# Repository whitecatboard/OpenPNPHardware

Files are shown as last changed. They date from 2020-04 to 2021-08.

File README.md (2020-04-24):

# Introduction

[Whitecat](https://whitecatboard.org) was created in 2016 as an ecosystem to provide hardware and software to everyone to deploy real IOT use cases in an easy way. Once the hardware was designed, we had to decide how to assemble it, and after analyzing various options we decided that, in a first stage, the best way was to produce our own units. Due to that, we started the construction of our own Pick&Place machine, based on [OpenBuilds](https://openbuilds.com), [OpenPNP](http://openpnp.org), and some custom hardware.

On this repository you will find all the relevant information about our P&P machine, such as custom hardware, 3D printed parts models, and more.

## Project parts

* The machine
* Control board
* [Feeders](https://github.com/whitecatboard/OpenPNPHardware/tree/master/feeder)

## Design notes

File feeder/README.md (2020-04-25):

# Introduction

Feeders have the responsibility to supply components to the machine. To have a high quality, in all the pick & place process, it's mandatory that feeders supply components in a reliable and precise way. Supplying a component is the first step of the pick & place process, so , the more precission on feeders, the more precission on the final place possition, because less corrections will be required in the next steps.

If you have enough money, you can buy feeders used in the industry by US $130 each. This was not our case, because:

* We need to mount at least 40 feeders on our machine, and we don't have US $5,200.
* Usually these feeders are pneumatic feeders, and a lot of additional noisy hardware is required (more money).

For the above reasons, we decided to work in our own feeder solution, after reviewing the [Volker Besmens's project](https://www.vbesmens.de/en/pick-and-place/automatic-feeder.html).

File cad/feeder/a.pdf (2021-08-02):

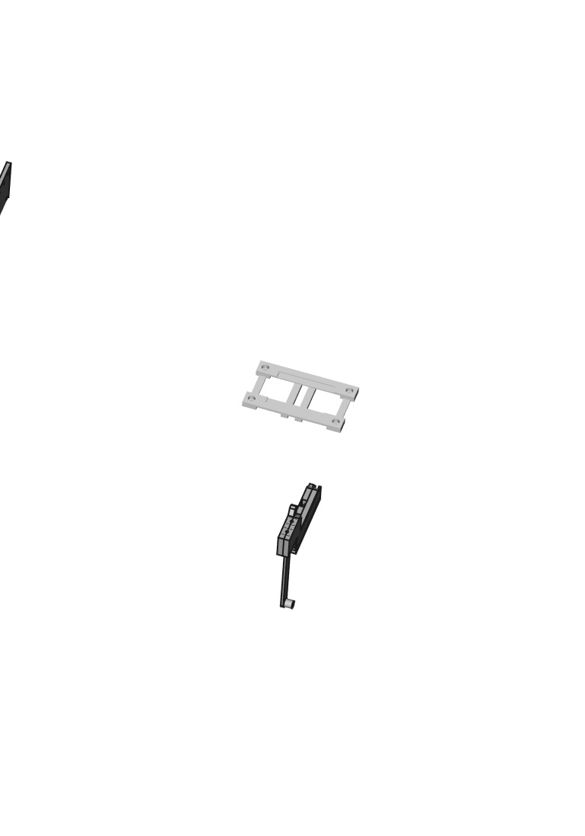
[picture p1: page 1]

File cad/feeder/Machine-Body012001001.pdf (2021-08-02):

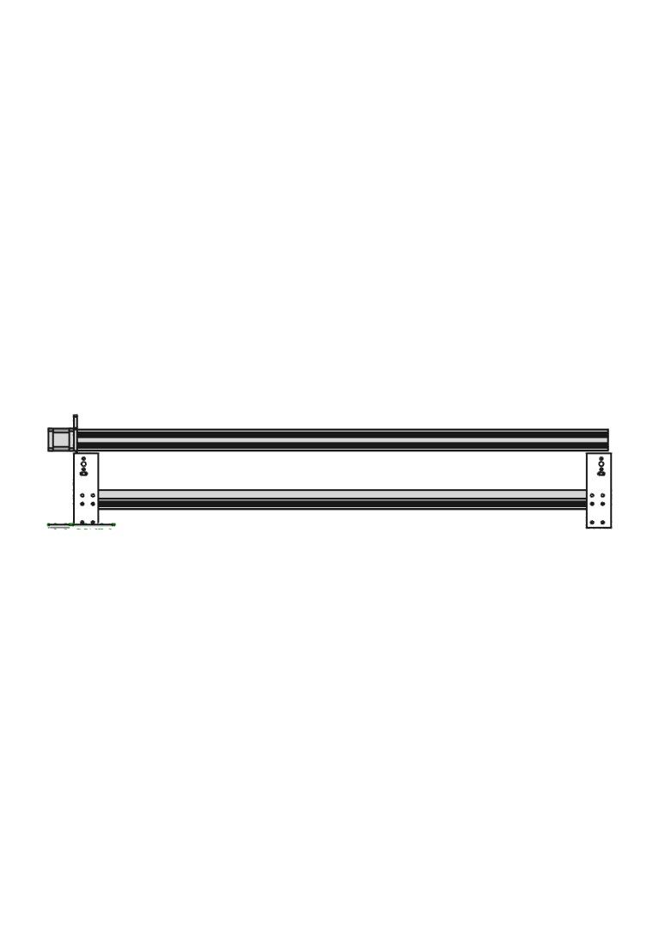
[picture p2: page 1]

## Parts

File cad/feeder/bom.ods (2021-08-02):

Description | Unit Price | Units | Total | Category
V-Slot 20x40x500mm Linear Rail | 6.06 | 4 | 24.23 | Frame
V-Slot 20x20x1000mm Linear Rail | 8.83 | 2 | 17.65 | Frame
V-Slot 20x40x1000mm Linear Rail | 12.11 | 1 | 12.11 | X-Axis
V-Slot 20x80x1000mm Linear Rail | 18.70 | 4 | 74.81 | Bed
12V Power Supply 33A 400W | 29.78 | 1 | 29.78 | Electronics
24V Power Supply 17A 400W | 39.48 | 1 | 39.48 | Electronics
NEMA 17 Stepper Motor 1.68A Bipolar 4 wires 77oz | 14.05 | 4 | 56.20 | Electronics
 |  |  | 254.26

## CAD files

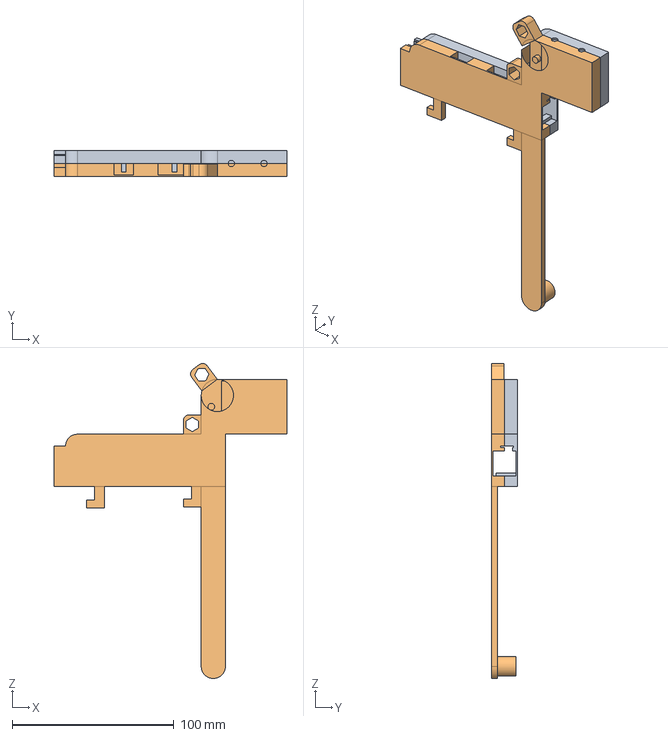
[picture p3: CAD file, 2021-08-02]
cad/feeder/Feeder2-Body001002Boolean.step
144.0 x 16.0 x 195.0 mm
Right001
Left001

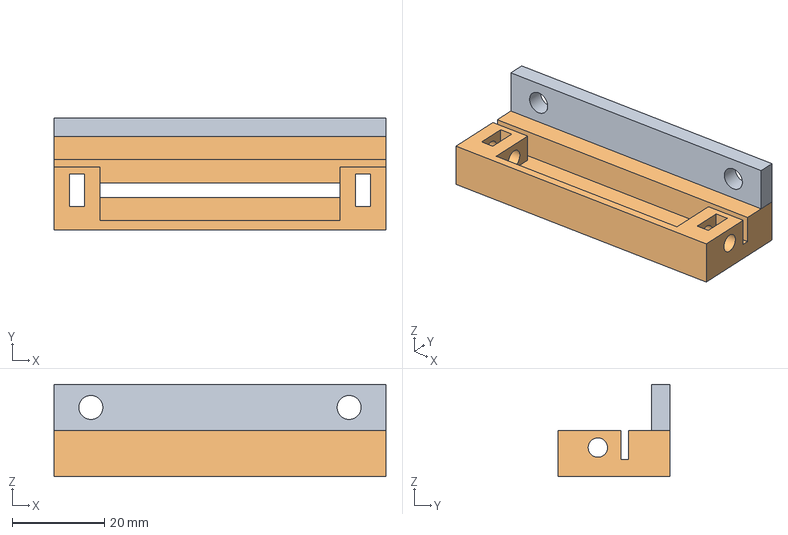
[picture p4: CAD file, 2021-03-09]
cad/head/BeltTensor.step
72.0 x 24.2 x 20.0 mm

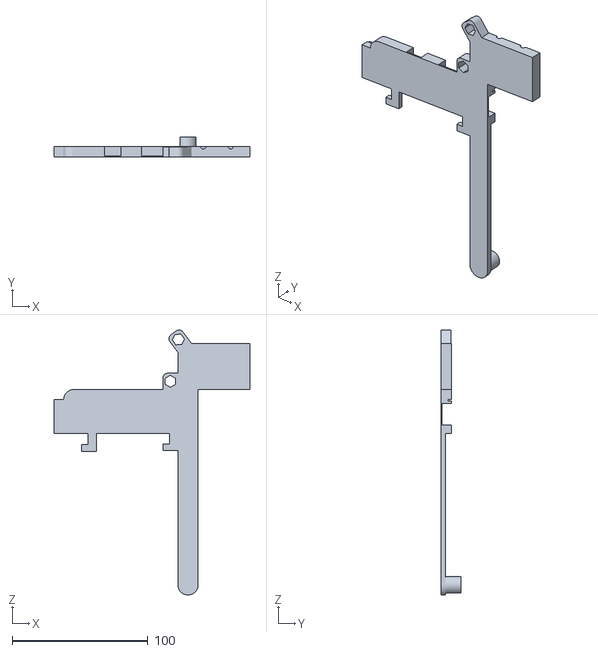
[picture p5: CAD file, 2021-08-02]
feeder/stl/Feeder_8mm_Left_1.0_mm_tape.stl
144.0 x 15.0 x 195.0

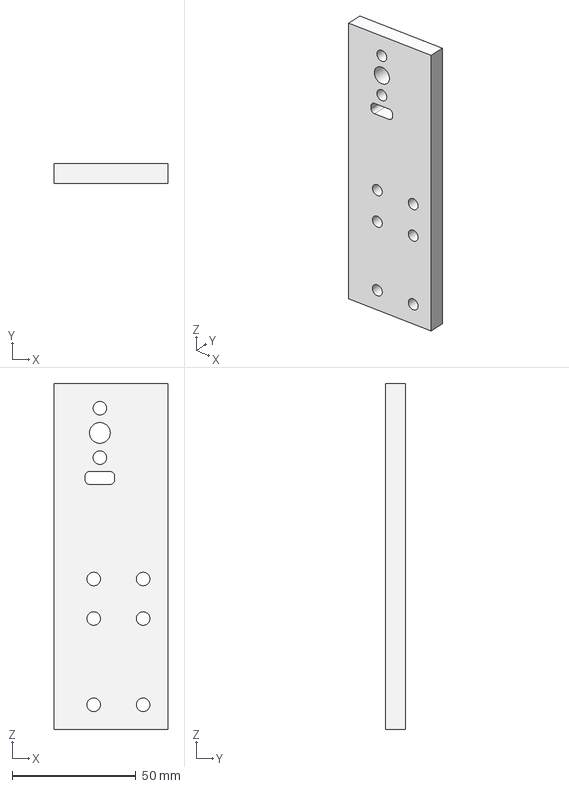
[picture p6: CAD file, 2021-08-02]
cad/feeder/WHC-DESK-PNP-FRM-PLT.step
46.0 x 8.00 x 140.0 mm

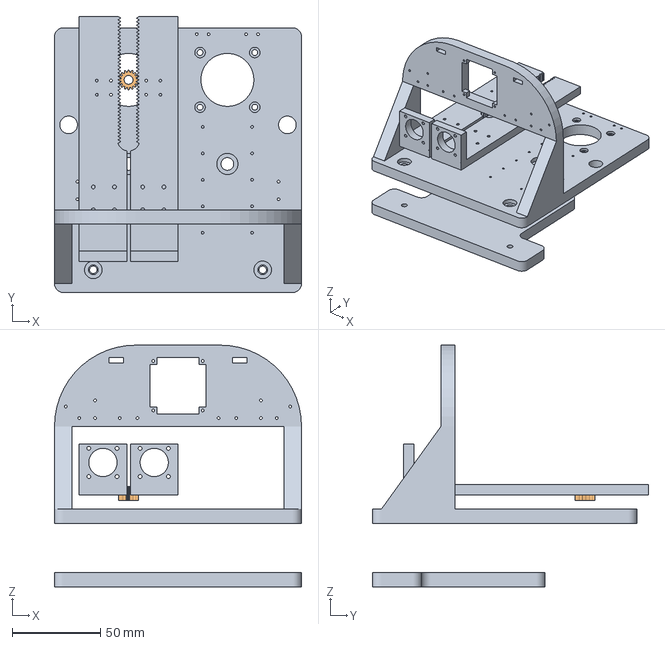
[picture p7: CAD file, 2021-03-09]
cad/head/Head.FCStd
140.0 x 156.4 x 137.0 mm
gear

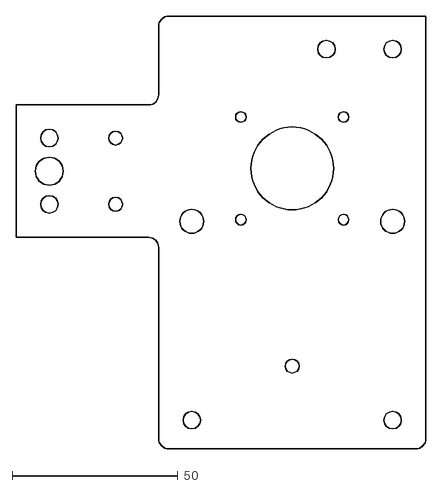
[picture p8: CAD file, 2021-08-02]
cad/feeder/Machine-X-Axis Plate.dxf
123.6 x 130.6

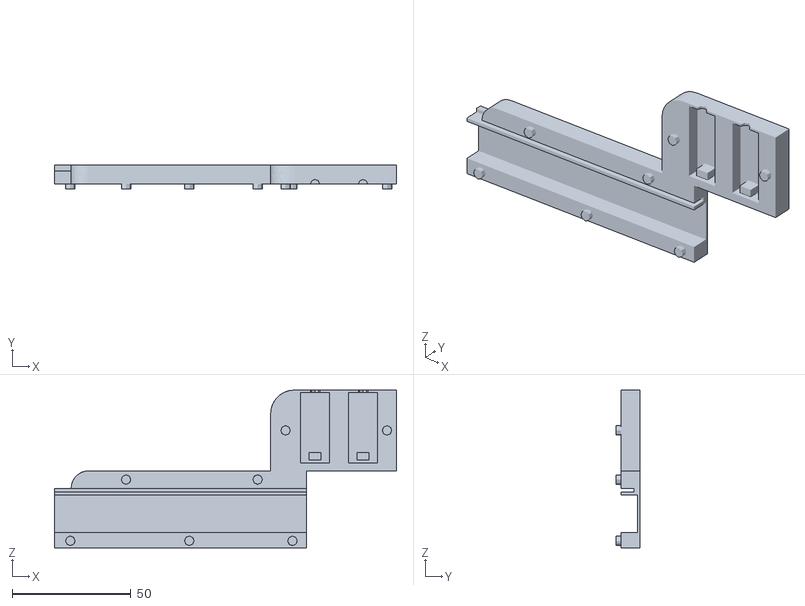
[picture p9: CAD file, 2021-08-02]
feeder/stl/Feeder_8mm_Right_1.5_mm_tape.stl
144.0 x 10.0 x 66.5

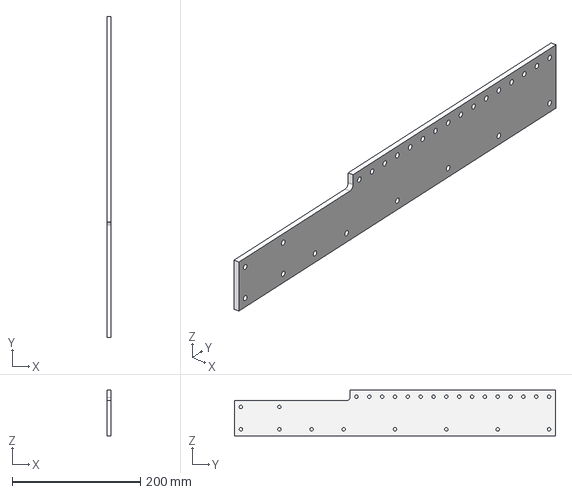
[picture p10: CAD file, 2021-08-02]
cad/feeder/Side Cover.step
6.00 x 500.0 x 70.9 mm

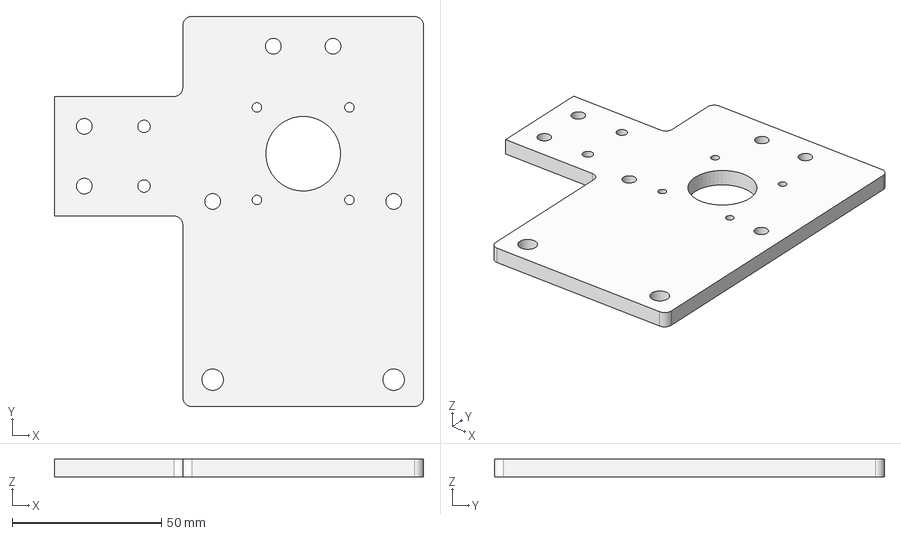
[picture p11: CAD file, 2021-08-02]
cad/feeder/Machine-Body012001001.step
123.6 x 130.6 x 6.00 mm

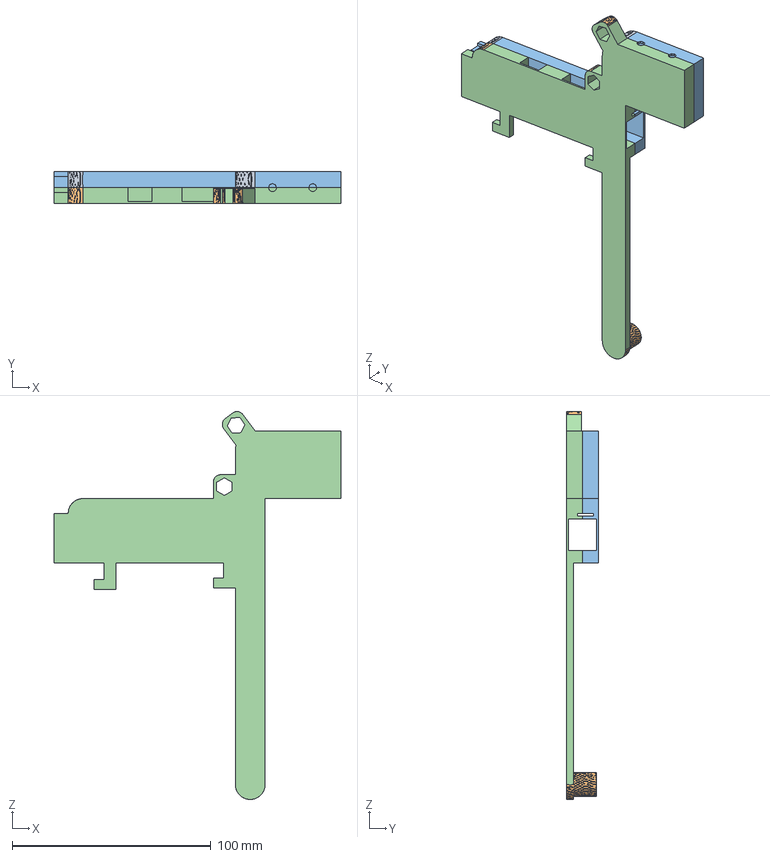
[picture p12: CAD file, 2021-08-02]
cad/feeder/Feeder2.FCStd
144.0 x 16.0 x 195.0 mm
Right001
Left001
Right001 (Meshed)
Left001 (Meshed)

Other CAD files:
feeder/stl/Feeder_8mm_Left_1.5_mm_tape.stl
feeder/stl/Feeder_8mm_Right_0.6_mm_tape.stl
feeder/stl/Feeder_8mm_Right_1.0_mm_tape.stl
cad/feeder/WHC-DESK-PNP-SIDE-COV.step
feeder/stl/Feeder_8mm_Left_1.2_mm_tape.stl
feeder/stl/Feeder_8mm_Right_1.2_mm_tape.stl
cad/feeder/Plate.step
feeder/stl/Feeder_8mm_Left_0.6_mm_tape.stl
cad/feeder/Machine-Body012001001.dxf
cad/feeder/Machine-Front Left Plate Frame001.dxf
cad/feeder/bed.step
feeder/stl/Cover_Tape_Reel_8mm.stl
feeder/stl/Feeder_8mm_Frame_fix.stl
feeder/stl/Feeder_8mm_Power_Supply_Frame_Fix.stl
feeder/stl/Tape_Reel_Stop.stl

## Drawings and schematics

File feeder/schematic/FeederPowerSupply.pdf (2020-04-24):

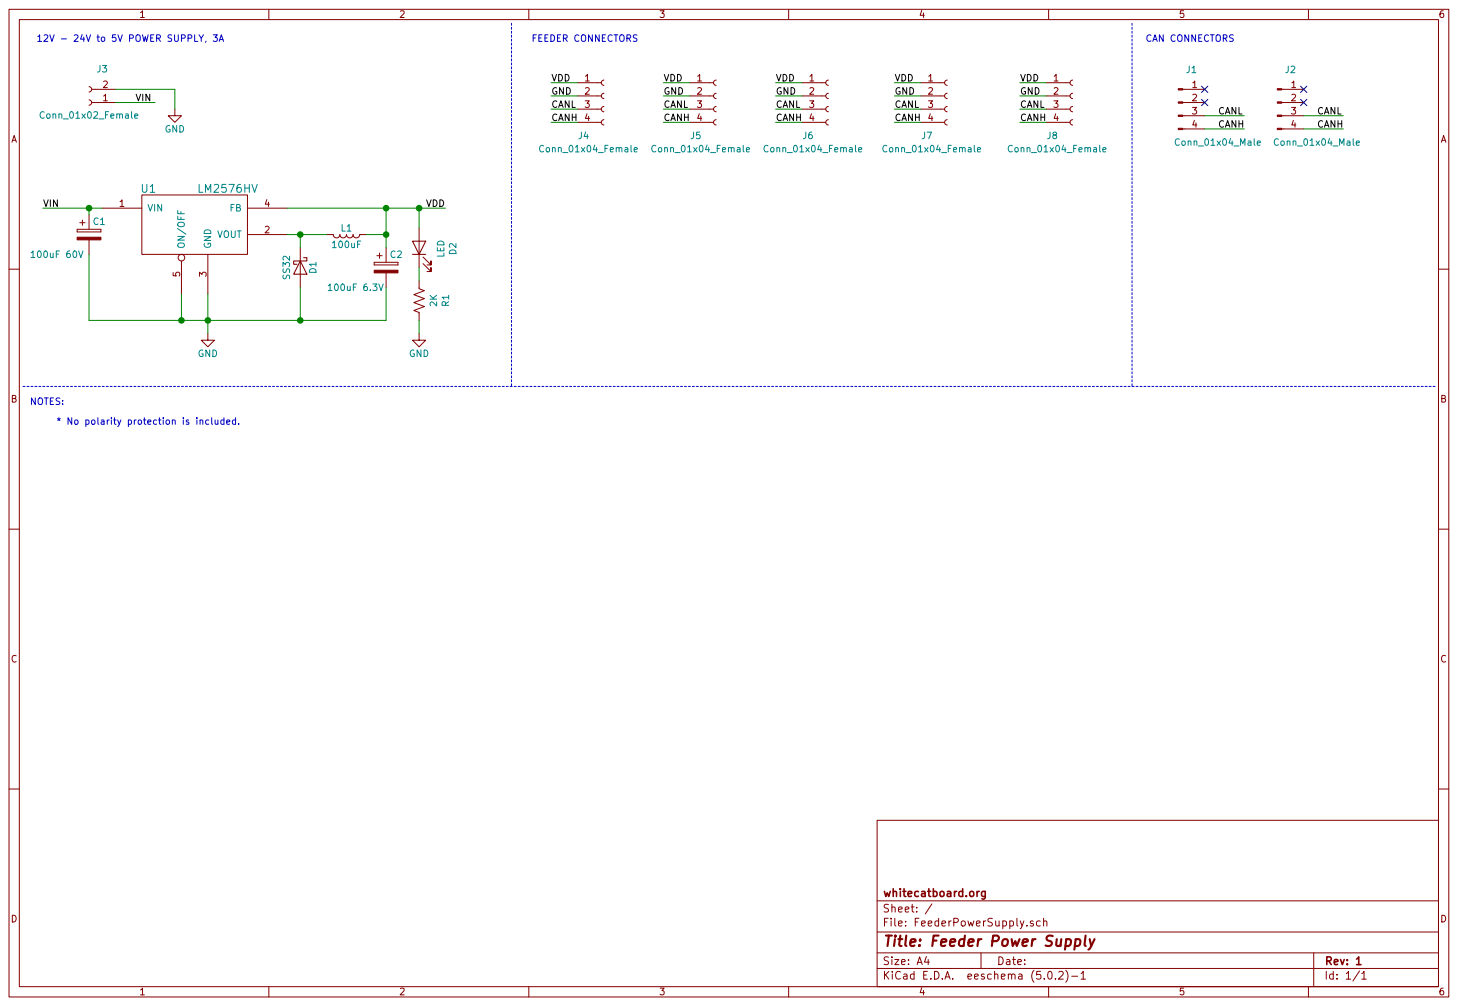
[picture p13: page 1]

J2 Conn_01x04_Male CANL CANH D2 LED 2KR1 GND

File: FeederPowerSupply.sch Sheet: / whitecatboard.org

Id: 1/1 Title: Feeder Power Supply

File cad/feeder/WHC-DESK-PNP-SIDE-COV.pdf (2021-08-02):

# All holes are non-threaded trough M5 holes

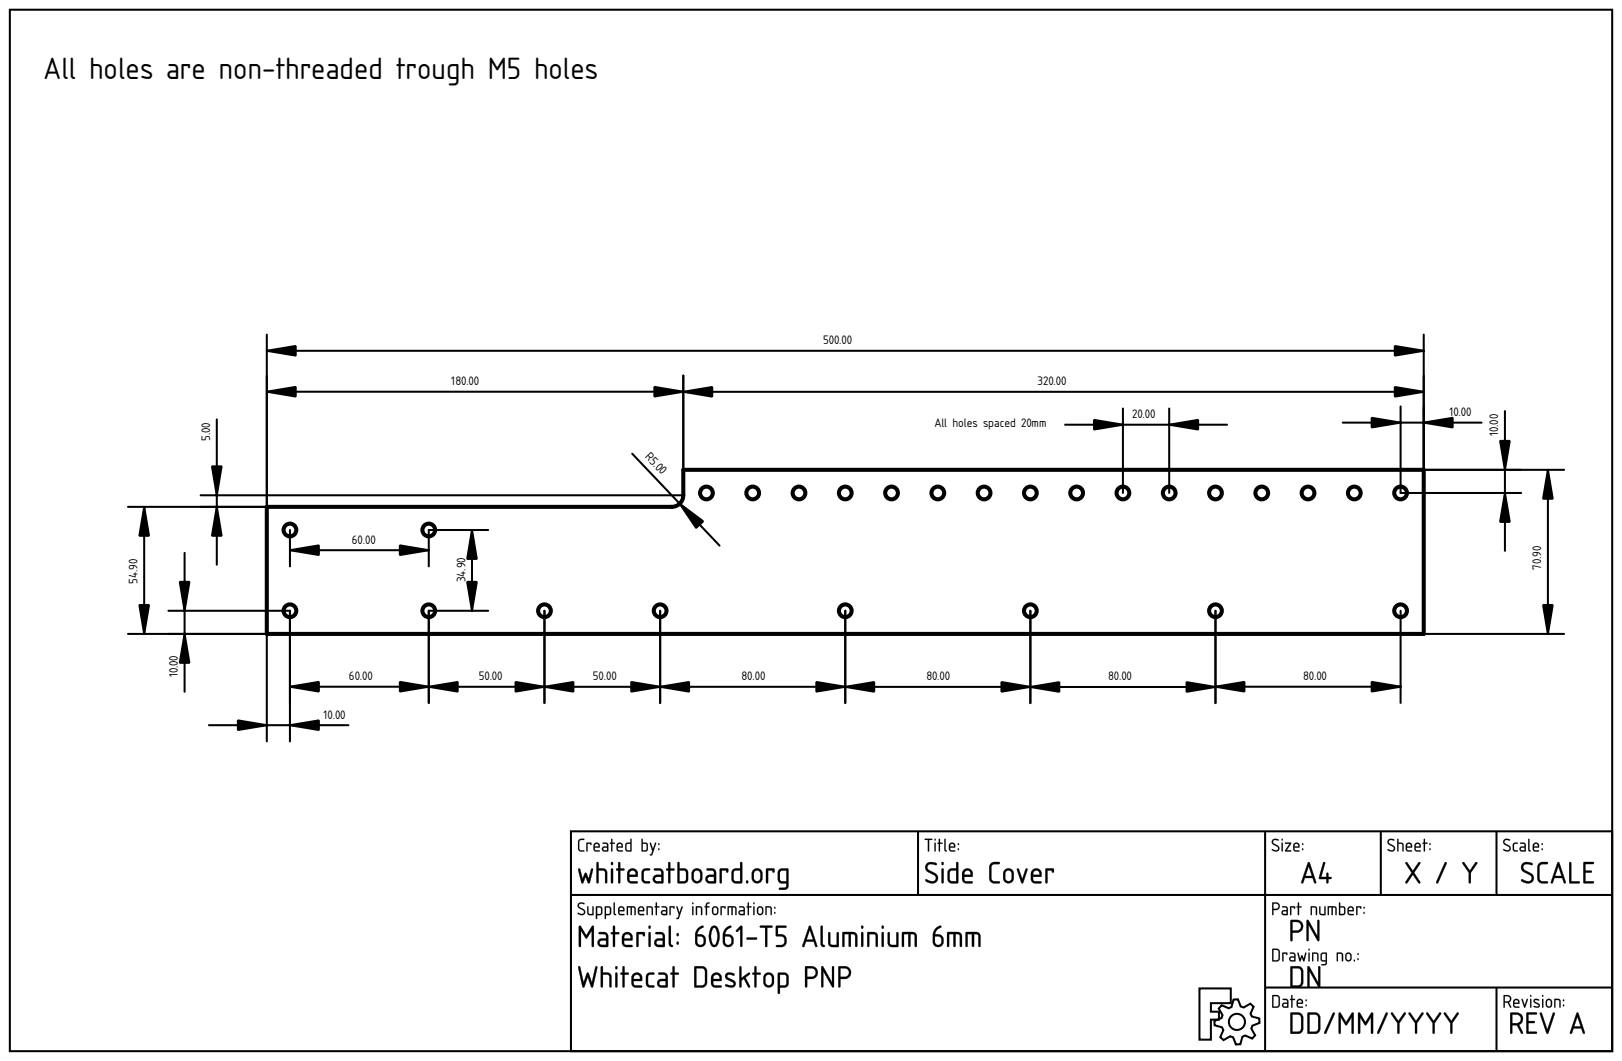
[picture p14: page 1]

All holes spaced 20mm

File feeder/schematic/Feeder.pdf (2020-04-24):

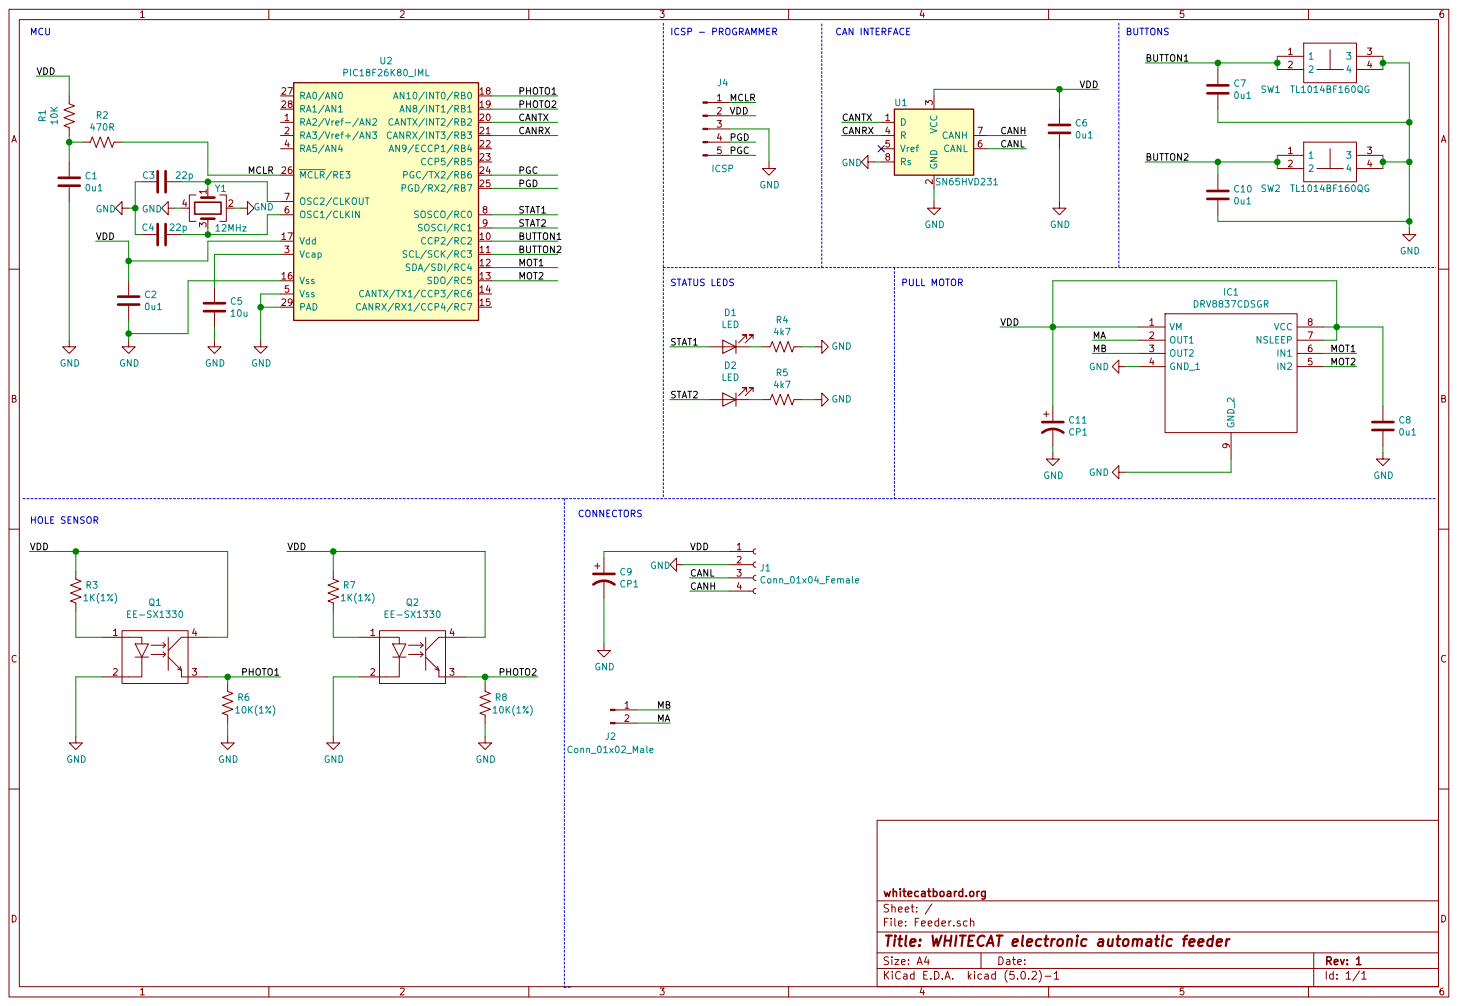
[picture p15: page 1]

Id: 1/1 Title: WHITECAT electronic automatic feeder File: Feeder.sch Sheet: / whitecatboard.org

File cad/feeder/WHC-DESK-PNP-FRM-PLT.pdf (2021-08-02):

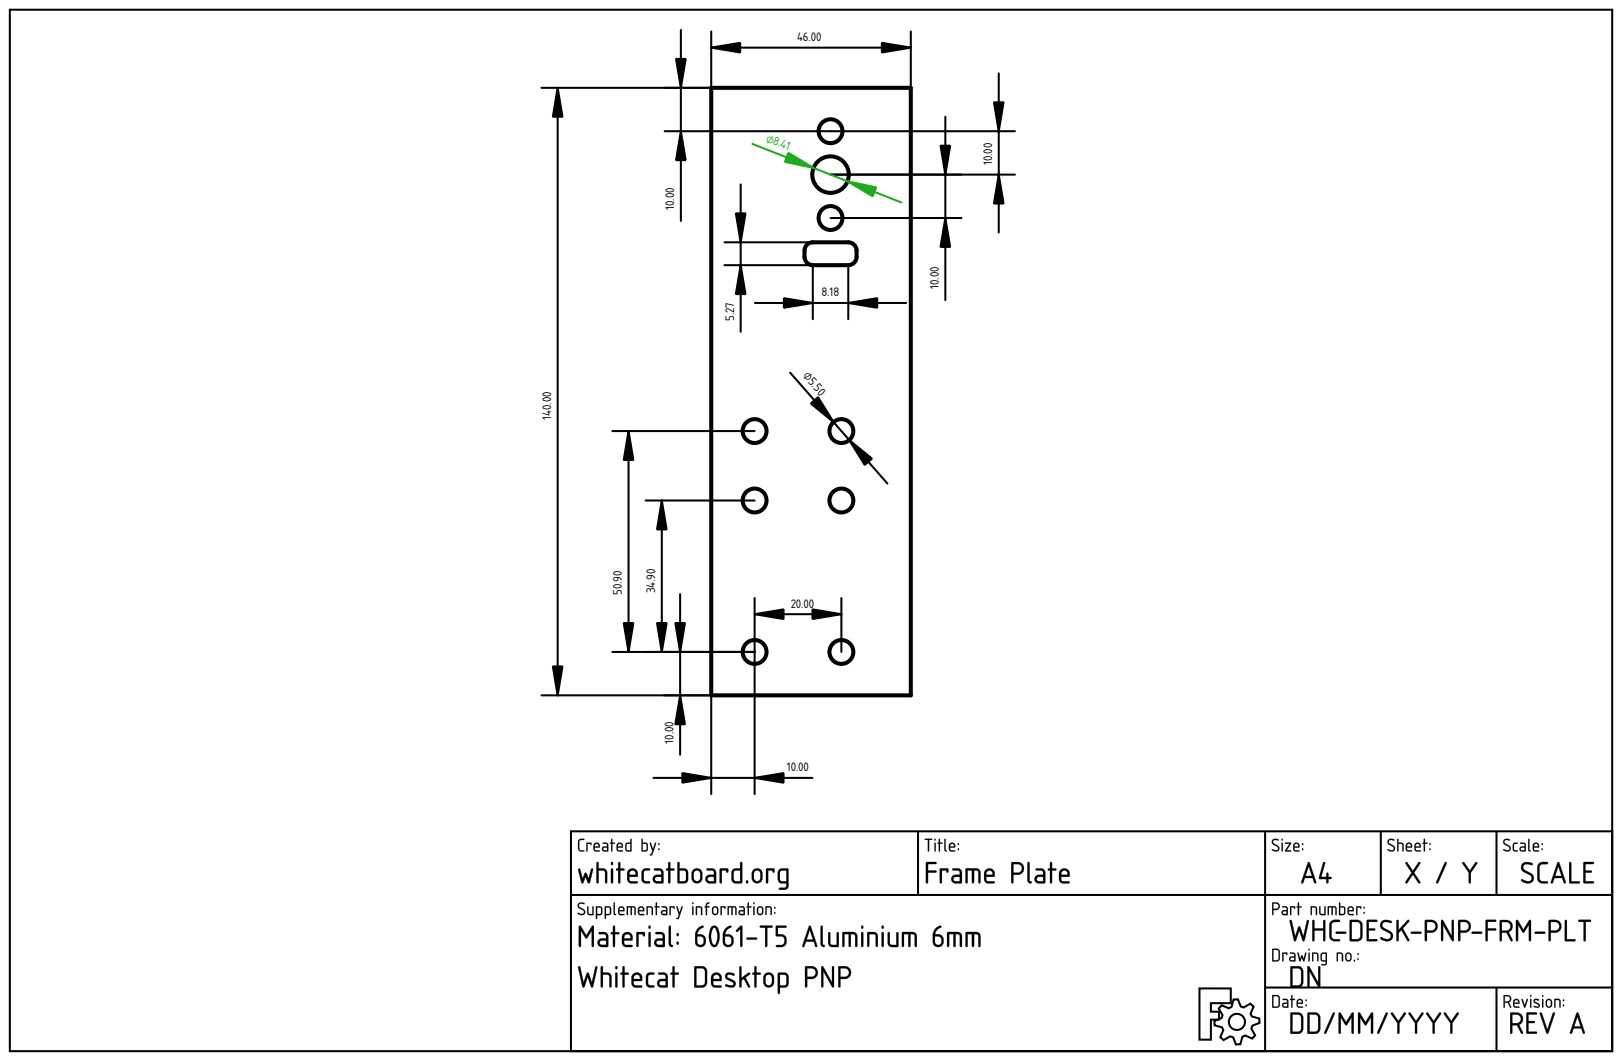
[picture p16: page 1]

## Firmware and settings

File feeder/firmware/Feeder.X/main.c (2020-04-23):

/*
 *          /\       /\
 *         /  \_____/  \
 *        /_____________\
 *        W H I T E C A T
 *
 * Copyright (C) 2020, IBEROXARXA SERVICIOS INTEGRALES, S.L.
 * Copyright (C) 2020, Jaume Olivé Petrus (jolive@whitecatboard.org)
 *
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
 * You should have received a copy of the GNU General Public License
 * along with this program.  If not, see <http://www.gnu.org/licenses/>.
 */

#include "gpio.h"
#include "can.h"
#include "task.h"
#include "motor.h"
#include "eeprom.h"

#include <xc.h>
#include <string.h>
#include <stdint.h>

// If no hole is detected within this time a feeder error will be triggered
#define FEED_TIMEOUT 1500

// EEPROM data
#define FEEDER_ID      0x0000 // Feeder id
#define FEEDER_PITCH   0x0001 // Feeder pitch
#define FEED_OK        0x0002 // Number of feed request OK
#define FEED_ERR       0x0006 // Number of feed request ERR

// Hardware mapping
#define STAT1_LED C0 // STAT1 led
#define STAT2_LED C1 // STAT2 led
#define MOTOR_CW  C5 // CW pin
#define MOTOR_CCW C4 // CCW pin
#define BUTTON1   C2 // Button 1
#define BUTTON2   C3 // Button 2
#define SWITCH1   B0 // Switch 1
#define SWITCH2   B1 // Switch 2

// Feeder status
typedef enum {
    StatusUnknown = 1,
    StatusPrevious = 2,
    StatusNotConfigured = 3,
    StatusWaitForConfig = 4,
    StatusReady = 5,
    StatusOnFeed = 6,
    StatusOnUnroll = 7,
    StatusDuplicatedId = 8,
} feeder_status_t;

// Feeder pitch types
typedef enum {
    Pitch_1_2 = 1, // Pitch 0.5
    Pitch_1,       // Pitch 1
    Pitch_2,       // Pitch 2
    Pitch_3,       // Pitch 3
    Pitch_4,       // Pitch 4
} feeder_pitch_t;

// Can message types
#define SERVICE_MSG 0x100
#define FEED_MSG    0X200
#define RESP_MSG    0x300
#define COUNT_MSG   0x301

// Service message
typedef enum {
    ServiceSetId = 1,
    ServiceSetPitch = 2,
    ServiceUpdate = 3,
    ServiceSaveCounters = 4,
    ServiceGetCounters = 5,
    ServiceResetCounters = 6,
} service_msg_type_t;

typedef struct {
    service_msg_type_t type; // Type of service message
    uint8_t data0;           // Message data 0
    uint8_t data1;           // Message data 1
} service_msg_t;

// Feed message
typedef struct {
    uint8_t feeder_id; // Feeder to perform feed operation
} feed_msg_t;

typedef struct {
    uint8_t feeder_id; // Feeder that has performed a feed operation
    uint8_t status;    // Feed operation status. 1 = ok, 0 = error
} feed_msg_response_t;

// Counter message
typedef struct {
    uint8_t feeder_id;
    uint8_t counter_id; // 1 = feed_ok, 2 = feed_err
    uint32_t value;
} counters_msg_t;

extern uint16_t _time_delta;
extern uint16_t _time_delta_led;
extern uint16_t _time_delta_button;

static uint8_t feeder_id = 0x00;
static feeder_pitch_t feeder_pitch = 0;

// Feeder status
static feeder_status_t status = StatusNotConfigured;
static feeder_status_t prev_status = StatusNotConfigured;

// Number of holes detected on current feed operation
static uint8_t detected_holes = 0;

// Number of holes required to get the next component for a feed operation
static uint8_t pitch_holes = 0;

// Counters
static uint32_t feed_ok = 0;
static uint32_t feed_err = 0;

static void update_status(feeder_status_t new_status) {
    if (new_status == StatusUnknown) {
        if (status != StatusDuplicatedId) {
            if ((feeder_id == 0) || (feeder_id == 0xff)) {
                if (status != new_status) {
                    prev_status = status;
                }
                
                status = StatusNotConfigured;
            } else {
                prev_status = StatusReady;
                status = StatusReady;
            }             
        }
        
        if ((feeder_pitch == 0) || (feeder_pitch == 0xff)) {
            // Default pitch
            feeder_pitch = Pitch_1;
            
            eeprom_write8(FEEDER_PITCH, feeder_pitch);
        }
        
        if (feed_ok == 0xffffffff) {
            feed_ok = 0;
        }
        
        if (feed_err == 0xffffffff) {
            feed_err = 0;
        }
    } else if (new_status == StatusPrevious) {
        status = prev_status;
    } else {
        if (status != new_status) {
            prev_status = status;
        }
        status = new_status;
    }
}

static uint8_t feed() {  
    uint8_t ok = 1;
    
    // Reset number of detected holes
    detected_holes = 0; 
    
    // Compute required number of holes to feed a component
    switch (feeder_pitch) {
        case Pitch_1_2: pitch_holes = 1; break;
        case Pitch_1:   pitch_holes = 1; break;
        case Pitch_2:   pitch_holes = 2; break;
        case Pitch_3:   pitch_holes = 3; break;
        case Pitch_4:   pitch_holes = 4; break;
    }    

    // Set timeout
    uint16_t timeout = FEED_TIMEOUT * pitch_holes;
    
    // Reset time
    _time_delta = 0;
    
    // Start move motor
    motor_ccw();

    while ((detected_holes < pitch_holes) && (ok)) {
        ok = _time_delta < timeout;
        
        asm("nop");
    }
    
    if (!ok) {
        // If timeout stop motor
        motor_stop();
    }    
    
    update_status(StatusPrevious);

    return ok;
}

static void unroll(void) {
    update_status(StatusOnUnroll);

    motor_cw();
    while (!gpio_pin_get(BUTTON2, 1));
    motor_stop();

    update_status(StatusPrevious);
}

static void process_feed_msg(can_frame_t *cf) {
    feed_msg_t msg;
    can_frame_t response;
    
    // Check that message size corresponds to a feed message
    if (cf->dlc == sizeof(feed_msg_t)) {
        // Get message
        memcpy(&msg, cf->data, cf->dlc);
        
        // Check that message is for us
        if (msg.feeder_id == feeder_id) {
            update_status(StatusOnFeed);    
            __delay_ms(5);
            task_disable();

            if (feed()) {
                feed_ok++;
                
                // Send response            
                response.sid = RESP_MSG;
                response.dlc = sizeof(feed_msg_response_t);
                response.data[0] = feeder_id;
                response.data[1] = 0x01;

                can_send(&response);                
            } else {
                feed_err++;
                
                // Send response            
                response.sid = RESP_MSG;
                response.dlc = sizeof(feed_msg_response_t);
                response.data[0] = feeder_id;
                response.data[1] = 0x00;

                can_send(&response);                                
            }
           
            task_enable();
        }
    }
}

static void process_service_msg(can_frame_t *cf) {
    service_msg_t msg;
    
    // Check that message size corresponds to a service message
    if (cf->dlc == sizeof(service_msg_t)) {
        // Get message
        memcpy(&msg, cf->data, cf->dlc);
        
        if ((msg.type == ServiceSetId) && (status == StatusWaitForConfig)) {
            feeder_id = msg.data0;
            
            eeprom_write8(FEEDER_ID, feeder_id);
            
            update_status(StatusUnknown);
        } else if ((msg.type == ServiceSetPitch) && (status == StatusReady)) {
            if (feeder_id == msg.data0) {
                feeder_pitch = msg.data1;
            
                eeprom_write8(FEEDER_PITCH, feeder_pitch);                
            }
        } else if ((msg.type == ServiceUpdate) && (status == StatusReady)) {
            if (msg.data0 == feeder_id) {
                asm("reset");
            }
        } else if ((msg.type == ServiceSaveCounters) && (status == StatusReady)) {
            if (msg.data0 == feeder_id) {
                eeprom_write32(FEED_OK, feed_ok);
                eeprom_write32(FEED_ERR, feed_err);
            }
        } else if ((msg.type == ServiceGetCounters) && (status == StatusReady)) {
           if (msg.data0 == feeder_id) {               
                // Send counters
                can_frame_t response;
                
                // feed_ok
                response.sid = COUNT_MSG;
                response.dlc = sizeof(counters_msg_t);
                response.data[0] = feeder_id;
                response.data[1] = 1;
                response.data[2] = (uint8_t)(feed_ok >> 24);
                response.data[3] = (uint8_t)(feed_ok >> 16);
                response.data[4] = (uint8_t)(feed_ok >> 8);
                response.data[5] = (uint8_t)(feed_ok);
                
                can_send(&response);                     

                // feed_err
                response.sid = COUNT_MSG;
                response.dlc = sizeof(counters_msg_t);
                response.data[0] = feeder_id;
                response.data[1] = 2;
                response.data[2] = (uint8_t)(feed_err >> 24);
                response.data[3] = (uint8_t)(feed_err >> 16);
                response.data[4] = (uint8_t)(feed_err >> 8);
                response.data[5] = (uint8_t)(feed_err);
                
                can_send(&response);   
                
                task_enable();
            }
        } else if ((msg.type == ServiceResetCounters) && (status == StatusReady)) {
           if (msg.data0 == feeder_id) {         
               feed_ok = 0;
               feed_err = 0;
               
               eeprom_write32(FEED_OK, feed_ok);
               eeprom_write32(FEED_ERR, feed_err);
           }      
        }
    }
}
                
static void leds(void) {
    if (status == StatusNotConfigured) {
        if (_time_delta_led > 125) {
            _time_delta_led = 0;
            gpio_pin_inv(STAT1_LED);
        }
        
        gpio_pin_clr(STAT2_LED);
    } else if (status == StatusWaitForConfig) {
        if (_time_delta_led > 250) {
            _time_delta_led = 0;
            gpio_pin_inv(STAT1_LED);
        }
        
        gpio_pin_clr(STAT2_LED);        
    } else if (status == StatusReady) {        
        _time_delta_led = 0;
        
        gpio_pin_set(STAT1_LED);        
        gpio_pin_clr(STAT2_LED);        
    } else if (status == StatusOnFeed) {
        _time_delta_led = 0;
        gpio_pin_set(STAT1_LED);        
        gpio_pin_set(STAT2_LED);        
    } else if (status == StatusOnUnroll) {
        _time_delta_led = 0;
        gpio_pin_clr(STAT1_LED);        
        gpio_pin_set(STAT2_LED);        
    } else if (status == StatusDuplicatedId) {
        if (_time_delta_led > 250) {
            _time_delta_led = 0;
            
            gpio_pin_inv(STAT1_LED);        
            gpio_pin_inv(STAT2_LED);                    
        }
    }
}

static void on_hole_1() {
    // Increment number of detectec holes
    detected_holes++;
    
    if (detected_holes >= pitch_holes) {
        // Stop motor
        motor_stop();        
    }        
    
    if (status == StatusReady) {
        gpio_pin_set(STAT2_LED);
        __delay_ms(50);
        gpio_pin_clr(STAT2_LED);
    }
}

static void on_hole_2() {
    if (feeder_pitch == Pitch_1_2) {
        // Increment number of detectec holes
        detected_holes++;

        if (detected_holes >= pitch_holes) {
            // Stop motor
            motor_stop();        
        }        

        if (status == StatusReady) {
            gpio_pin_set(STAT2_LED);
            __delay_ms(50);
            gpio_pin_clr(STAT2_LED);
        }        
    }
}

void schelude_tasks(void) {
    leds();
}

void main(void) {
    can_frame_t cf; // Current can frame

    // Init platform, default settings
    platform_init();
    
    // Init leds
    gpio_pin_output(STAT1_LED, 1);
    gpio_pin_output(STAT2_LED, 1);
    
    // Install an ISR on switches to detect when we are on a tape hole.
    // Tape holes are detected when a raising edge is detected.
    gpio_isr_attach(SWITCH1, on_hole_1, GPIOIntRaisingEdge);
    gpio_isr_attach(SWITCH2, on_hole_2, GPIOIntRaisingEdge);
    
    // Init motor
    motor_attach(MOTOR_CW, MOTOR_CCW);
    
    // Read configuration from EEPROM
    feeder_id = eeprom_read8(FEEDER_ID);
    feeder_pitch = eeprom_read8(FEEDER_PITCH);
    
    // Read counters
    feed_ok = eeprom_read32(FEED_OK);
    feed_err = eeprom_read32(FEED_ERR);
    
    // Init CAN
    can_setup_init();
    can_add_filter(SERVICE_MSG);
    can_add_filter(FEED_MSG);
    can_setup_end();

    // Init tasks
    task_init();
          
    update_status(StatusUnknown);
          
    while (1) {
        // Process CAN messages
        if (can_get(SERVICE_MSG, &cf)) {
            process_service_msg(&cf);
        }

        if (can_get(FEED_MSG, &cf) && (status == StatusReady)) {
            process_feed_msg(&cf);
        }
        
        // Process buttons
        if (((status == StatusNotConfigured) || (status == StatusDuplicatedId) || (status == StatusReady)) && (!gpio_pin_get(BUTTON1, 1))) {
            if ((status == StatusNotConfigured) || (status == StatusDuplicatedId)) {
                update_status(StatusWaitForConfig);
            } else if ((status == StatusReady)) {
                // How many time button is pressed
                uint16_t pressed_time;
                
                _time_delta_button = 0;

                while (!gpio_pin_get(BUTTON1, 1)) {
                    asm("nop");
                }
                
                pressed_time = _time_delta_button;
                
                if ((pressed_time >= 1000) && (pressed_time <= 2000)) {
                    if (status == StatusReady) {
                        update_status(StatusWaitForConfig);                    
                    }
                } else if (status == StatusReady) {
                    update_status(StatusOnFeed);    
                    __delay_ms(5);
                    task_disable();

                    feed();

                    task_enable();
                }                
            }
        }
        
        if ((status == StatusReady) && (!gpio_pin_get(BUTTON2, 1))) {
            unroll();
        }
    } 
}

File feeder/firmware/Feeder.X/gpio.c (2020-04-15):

/*
 *          /\       /\
 *         /  \_____/  \
 *        /_____________\
 *        W H I T E C A T
 *
 * Copyright (C) 2020, IBEROXARXA SERVICIOS INTEGRALES, S.L.
 * Copyright (C) 2020, Jaume Olivé Petrus (jolive@whitecatboard.org)
 *
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
 * You should have received a copy of the GNU General Public License
 * along with this program.  If not, see <http://www.gnu.org/licenses/>.
 */

#include "config.h"
#include "gpio.h"

#include <xc.h>

typedef struct {
    volatile unsigned char *tris;
    volatile unsigned char *lat;
    volatile unsigned char *port;
    volatile unsigned char *ansel;
    volatile unsigned char iomask;
    uint8_t achanmask;
    uint8_t anselmask;
} gpio_reg_t;
 
const gpio_reg_t gpio_reg[] = {
    {&TRISA,&LATA,&PORTA,&ANCON0, 1 << 0, 0 << 2, 1 << 0},
    {&TRISA,&LATA,&PORTA,&ANCON0, 1 << 1, 1 << 2, 1 << 1},
    {&TRISA,&LATA,&PORTA,&ANCON0, 1 << 2, 2 << 2, 1 << 2},
    {&TRISA,&LATA,&PORTA,&ANCON0, 1 << 3, 3 << 2, 1 << 3},
    {&TRISA,&LATA,&PORTA,0x0000,  1 << 4, 0xff, 0xff},
    {&TRISA,&LATA,&PORTA,0x0000,  1 << 5, 0xff, 0xff},
    {&TRISA,&LATA,&PORTA,0x0000,  1 << 6, 0xff, 0xff},
    {&TRISA,&LATA,&PORTA,0x0000,  1 << 7, 0xff, 0xff},

    {&TRISB,&LATB,&PORTB,&ANCON1, 1 << 0, 10 << 2, 1 << 2},
    {&TRISB,&LATB,&PORTB,&ANCON1, 1 << 1, 8 << 2, 1 << 0},
    {&TRISB,&LATB,&PORTB,0x0000, 1 << 2, 0xff, 0xff},
    {&TRISB,&LATB,&PORTB,0x0000, 1 << 3, 0xff, 0xff},
    {&TRISB,&LATB,&PORTB,&ANCON1, 1 << 4, 9 << 2, 1 << 1},
    {&TRISB,&LATB,&PORTB,0x0000, 1 << 5, 0xff, 0xff},
    {&TRISB,&LATB,&PORTB,0x0000, 1 << 6, 0xff, 0xff},
    {&TRISB,&LATB,&PORTB,0x0000, 1 << 7, 0xff, 0xff},

    {&TRISC,&LATC,&PORTC,0x0000, 1 << 0, 0xff, 0xff},
    {&TRISC,&LATC,&PORTC,0x0000, 1 << 1, 0xff, 0xff},
    {&TRISC,&LATC,&PORTC,0x0000, 1 << 2, 0xff, 0xff},
    {&TRISC,&LATC,&PORTC,0x0000, 1 << 3, 0xff, 0xff},
    {&TRISC,&LATC,&PORTC,0x0000, 1 << 4, 0xff, 0xff},
    {&TRISC,&LATC,&PORTC,0x0000, 1 << 5, 0xff, 0xff},
    {&TRISC,&LATC,&PORTC,0x0000, 1 << 6, 0xff, 0xff},
    {&TRISC,&LATC,&PORTC,0x0000, 1 << 7, 0xff, 0xff}
};

#if INCLUDE_GPIO_EXTERNAL_INTERRUPTS
static void dummy() { return ; }

gpio_isr_func_t gpio_isr[] = {
    dummy,
    dummy,
    dummy,
    dummy
};
#endif

void gpio_pin_input(uint8_t pin) {
    *gpio_reg[pin].tris |= gpio_reg[pin].iomask;
    
    if (gpio_reg[pin].anselmask != 0xff) {
        *gpio_reg[pin].ansel &= (uint8_t)~gpio_reg[pin].anselmask;
    }
}

void gpio_pin_output(uint8_t pin, uint8_t set) {
    if (set) {
        *gpio_reg[pin].lat |= (uint8_t)gpio_reg[pin].iomask;
    } else {
        *gpio_reg[pin].lat &= (uint8_t)~gpio_reg[pin].iomask;
    }
    
    *gpio_reg[pin].tris &= (uint8_t)~gpio_reg[pin].iomask;

   if (gpio_reg[pin].anselmask != 0xff) {
        *gpio_reg[pin].ansel &= (uint8_t)~gpio_reg[pin].anselmask;
    }
}

void gpio_pin_analog(uint8_t pin) {
    if (gpio_reg[pin].achanmask != 0xff) {        
        ADCON1bits.VCFG =  0X00;  // vref+ = AVDD
        ADCON1bits.VNCFG = 0X00;  // vref- = AVSS
        ADCON1bits.CHSN =  0x00;  // No negative channels
        
        ADCON2bits.ADFM =  1;     // Right justified
        ADCON2bits.ACQT =  0x02;  // 4 TAD
        ADCON2bits.ADCS =  0x02;  // FOSC/32
        
        // Configure as analog
        gpio_pin_input(pin);
        *gpio_reg[pin].ansel |= (uint8_t)gpio_reg[pin].anselmask;
      
        // Enable module
        ADCON0bits.ADON = 1;
   }
}

uint16_t gpio_pin_get_analog(uint8_t pin) {
    if (gpio_reg[pin].achanmask != 0xff) {
        // Enable channel
        ADCON0 |= gpio_reg[pin].achanmask;
        
        // Start conversion
        ADCON0bits.GO = 1;
        
        // Wait for converssion
        while (ADCON0bits.DONE) {
            asm("nop");
        }

        // Disable channel
        ADCON0 &= ~gpio_reg[pin].achanmask;
        
        // Read conversion
        return ((ADRESH<<8) | (ADRESL));
    }
    
    return 0;
}

void gpio_pin_set_val(uint8_t pin, uint8_t val) {
    if (val) {
        *gpio_reg[pin].lat |= (uint8_t)gpio_reg[pin].iomask;
    } else {
        *gpio_reg[pin].lat &= (uint8_t)~gpio_reg[pin].iomask;        
    }
}

void gpio_pin_set(uint8_t pin) {
    *gpio_reg[pin].lat |= (uint8_t)gpio_reg[pin].iomask;
}

void gpio_pin_clr(uint8_t pin) {
    *gpio_reg[pin].lat &= (uint8_t)~gpio_reg[pin].iomask;
}

void gpio_pin_inv(uint8_t pin) {
    *gpio_reg[pin].lat ^= (uint8_t)gpio_reg[pin].iomask;
}
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

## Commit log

2020-04-15 Added stl files for 8 mm feeder, 0.9 mm tape height
    [Left_8mm_0.9_mm_tape.stl]
2020-04-15 Added tape reel stop and cober tape reel form 8mm tapes
    [Feeder_tape_stop.stl, Reel_8mm.stl]
2020-04-15 Minor bugs
    [Left_8mm_0.9_mm_tape.stl]
2020-04-15 Feeder Firmware, added service message to set feeder pitch
2020-04-23 Add more feeder parts
    [Feeder_tape_stop.stl, Fix_Frame_8mm.stl, Left_8mm_0.6_mm_tape.stl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]
2020-04-24 Added feeder schematic
2020-04-24 Added Feeder Power Supply schematic
2020-04-24 Minor bugs
    * Updated Ender 3 files / hole supports removed
    * Renamed STL files for clarification
    * Removed duplicated STL files
    [Cover_Tape_Reel_8mm.stl, Feeder_8mm_Frame_fix.stl, Feeder_8mm_Left_0.6_mm_tape.stl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]
2020-04-24 Added Feeder 8mm Power Supply Frame Fix STL model
    [Feeder_8mm_Power_Supply_Frame_Fix.stl]
2020-07-29 Added Head CAD files
    [Head.FCStd]
2020-07-29 PNP Head CAD minor changes
    [Head.FCStd]
2021-03-09 Minor changes
    [BeltTensor.step, Head.FCStd]
2021-08-02 General update
    [Feeder2-Body001002Boolean.step, Feeder2.FCStd, Feeder_8mm_Left_0.6_mm_tape.stl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]

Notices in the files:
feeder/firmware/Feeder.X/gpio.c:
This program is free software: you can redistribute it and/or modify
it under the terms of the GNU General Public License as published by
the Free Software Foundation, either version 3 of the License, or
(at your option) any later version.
